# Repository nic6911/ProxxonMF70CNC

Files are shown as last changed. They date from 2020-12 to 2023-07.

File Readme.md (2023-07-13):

# Proxxon MF70 CNC
CNC conversion for the Proxxon MF70 based on 3D printed files.
Electronics embedded in Z-axis column !

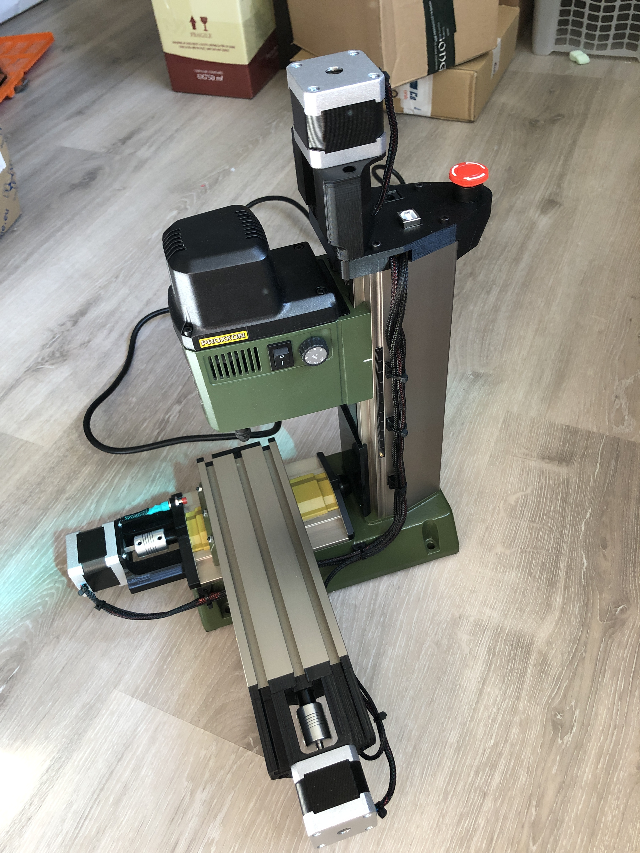
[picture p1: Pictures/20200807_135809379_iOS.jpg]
Machine


If you like then please

"Buy Me A Coffee" (https://bmc.link/nic6911w)

## BOM
Arduino UNO  
GRBL Shield w. 3 x drivers  
Braided cable sleeving  
Double adhesive tape for cable-tie mount  
3 x Alu flex coupler 5x5 mm shafts and outer measurements: 19x25mm  
E-stop button for 16mm panel cut-out. 23.5mm diameter button  
6 x F5-12M bearing  
3 x 7 mm push button switches for endstop SPST PBS-110  
12 x M3x6 for motor mount  
6 x M4x35 for mounting brackets  
6 x M4 SL nut  
3 x small screws for mounting Arduino  
3 x NEMA 17 stepper motors  
Wires and connectors as needed for switches and motors  

Printed parts:  
6 x cable_tie_mount  
3 x spacer_xyz  
1 of each of the remaining files  

## Software
GRBL and OpenBuilds Control software. My GRBL settings can be found in "grbl-settings-backup.txt"

## How To
Print the parts  
Measure up lengths of wires for motors and switches (make them somewhat longer than needed to be sure) and solder things up to get the extended cabling needed  
Disassemble the x, y and z-axis of the proxxon  
Remove the xyz handles from the lead screws  
F5-12M bearings goes in both ends on the x and y-axes and on the z-axis it there is one on both sides of the printed z-axis mount  
Only the original proxxon plastic part on the motor side is replaced on the x and y-axes  
A grooving in the 3D printed parts for the x and y-axes takes the metal plate from the original proxxon part  
Mount motors and end-switches on the x and y-axes motor mounts  
When a bearing has been placed in both ends of the x and y-axes the the motor mounts can be added to the x and y-axes (remember spacer and flex coupling)  
Make sure there is a little tension on the flex-coupler up against the spacer that pushes on the F5-12M bearing  
  
This work is licensed under a
[Creative Commons Attribution-ShareAlike 4.0 International License][cc-by-sa].

[][cc-by-sa]

[cc-by-sa]: http://creativecommons.org/licenses/by-sa/4.0/
[cc-by-sa-image]: https://licensebuttons.net/l/by-sa/4.0/88x31.png
[cc-by-sa-shield]: https://img.shields.io/badge/License-CC%20BY--SA%204.0-lightgrey.svg

Find more of my work here:  
https://youtube.com/user/wan46696  
https://www.instructables.com/member/nicengineering/

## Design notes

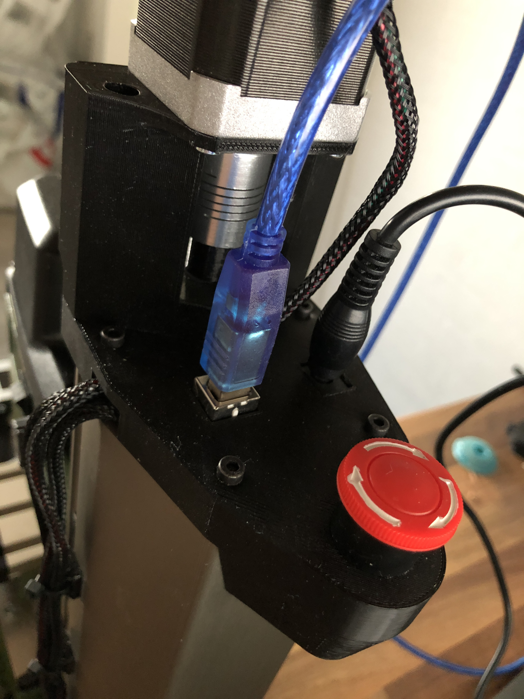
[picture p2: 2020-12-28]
Pictures/20200811_183554496_iOS.jpg

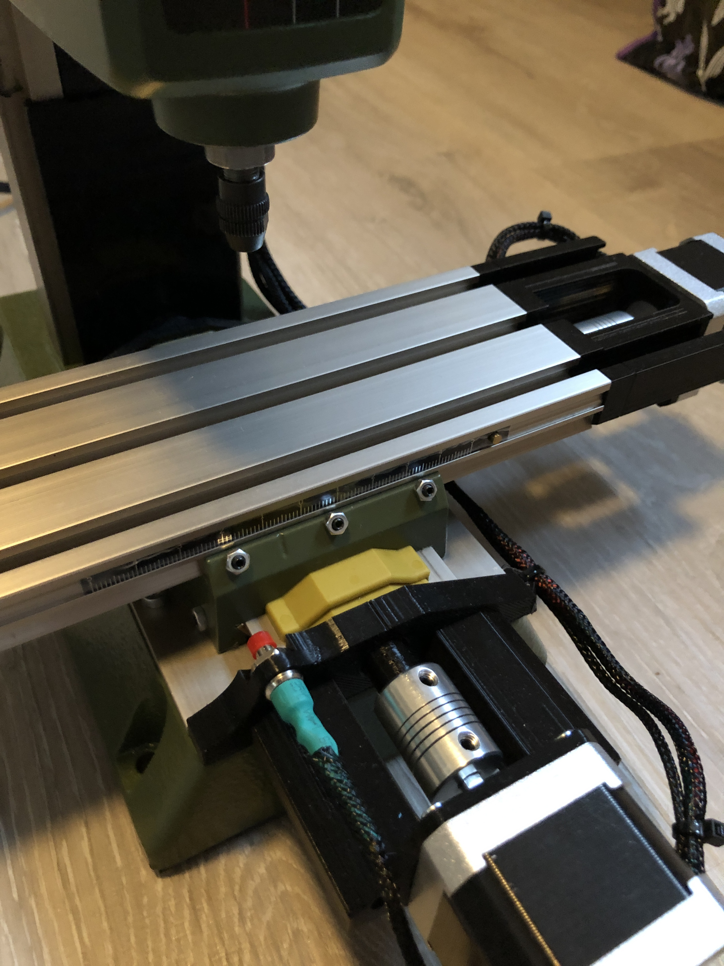
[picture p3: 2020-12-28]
Pictures/20200811_184021557_iOS.jpg

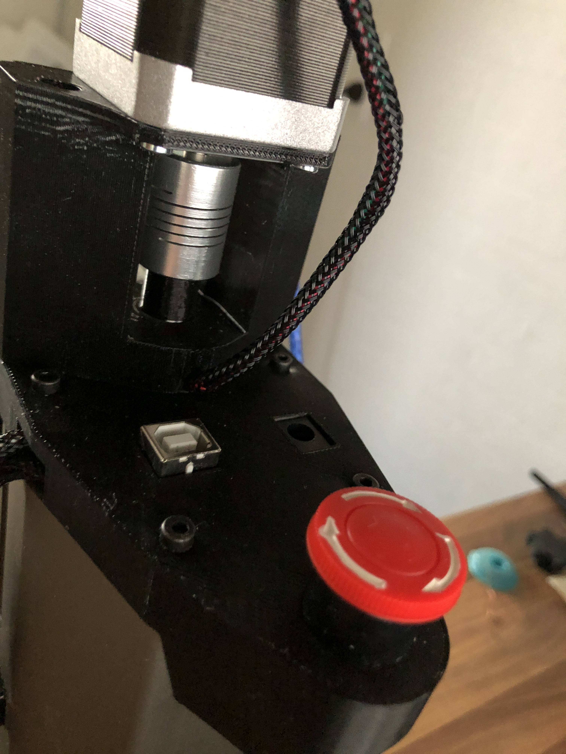
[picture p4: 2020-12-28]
Pictures/20200811_183607220_iOS.jpg

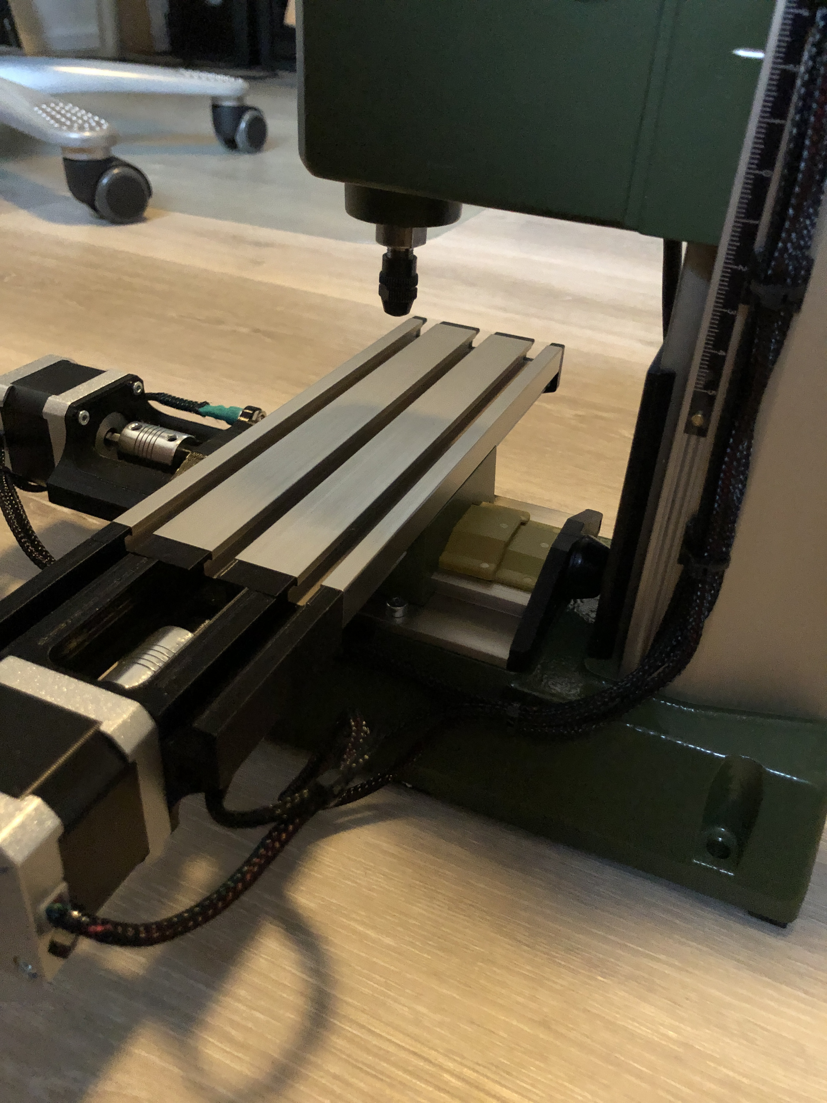
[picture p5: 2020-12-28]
Pictures/20200811_184040047_iOS.jpg

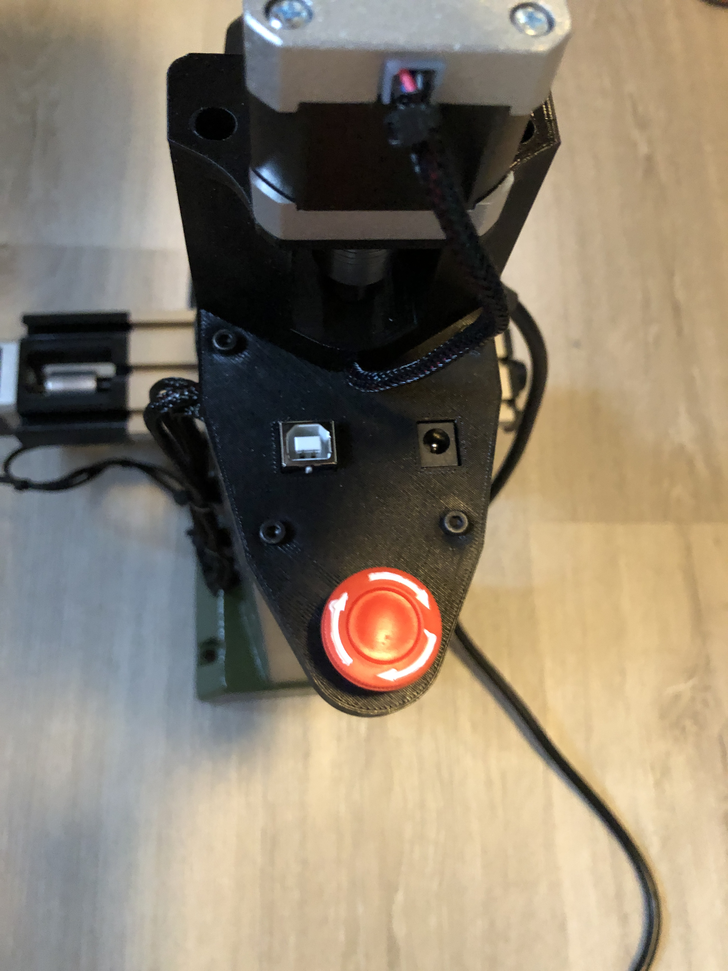
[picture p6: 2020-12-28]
Pictures/20200811_184008674_iOS.jpg

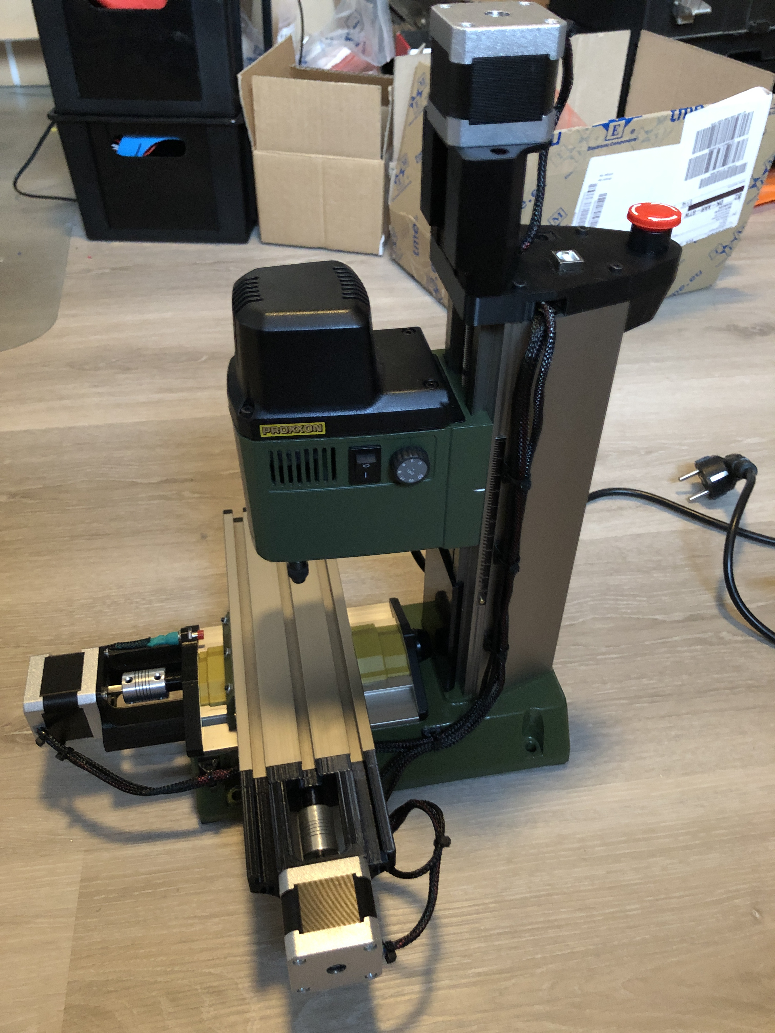
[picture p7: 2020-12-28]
Pictures/20200811_184046777_iOS.jpg

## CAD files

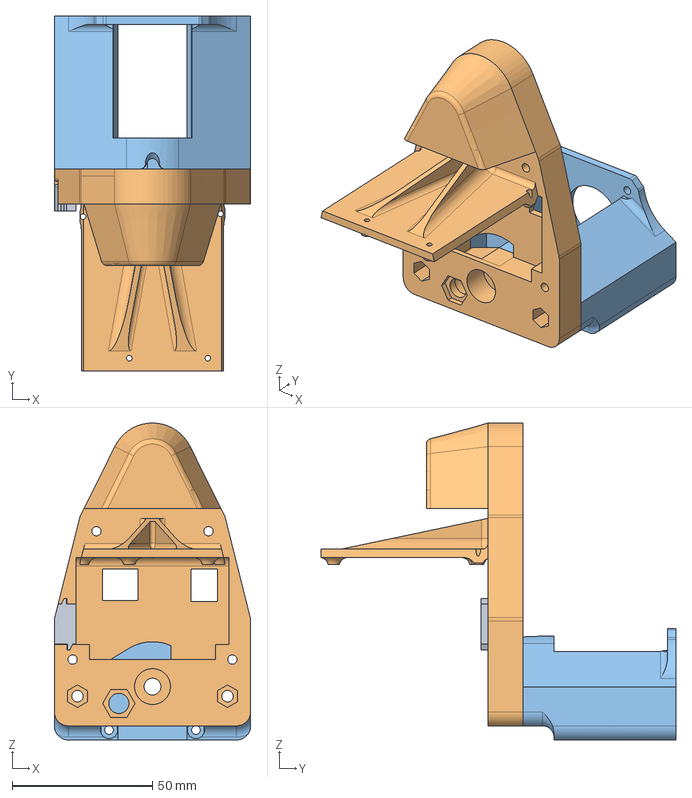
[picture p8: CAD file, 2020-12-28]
STEP/Z-axis_mount.step
70.0 x 126.5 x 113.0 mm

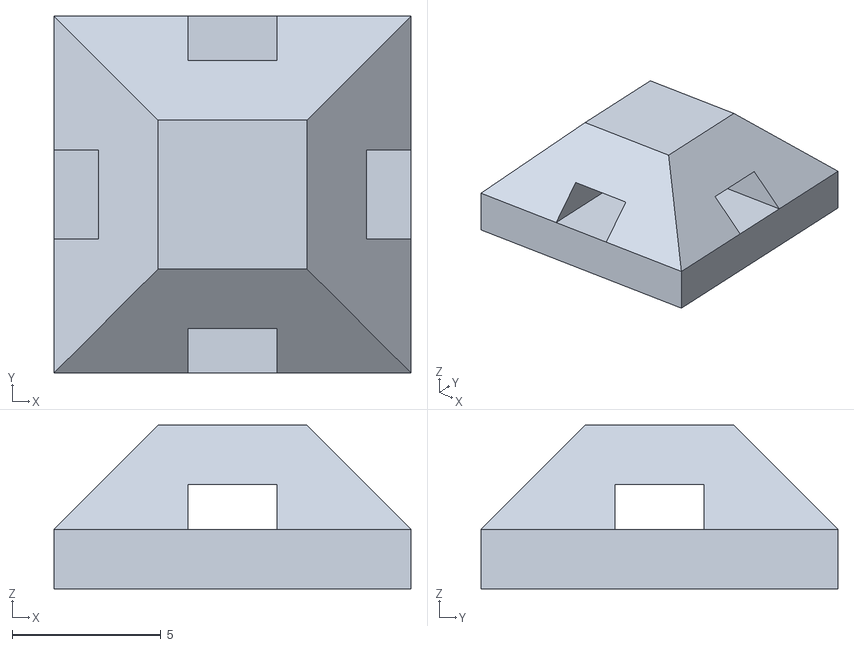
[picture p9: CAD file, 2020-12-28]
STL/cable_tie_mount.stl
12.0 x 12.0 x 5.50

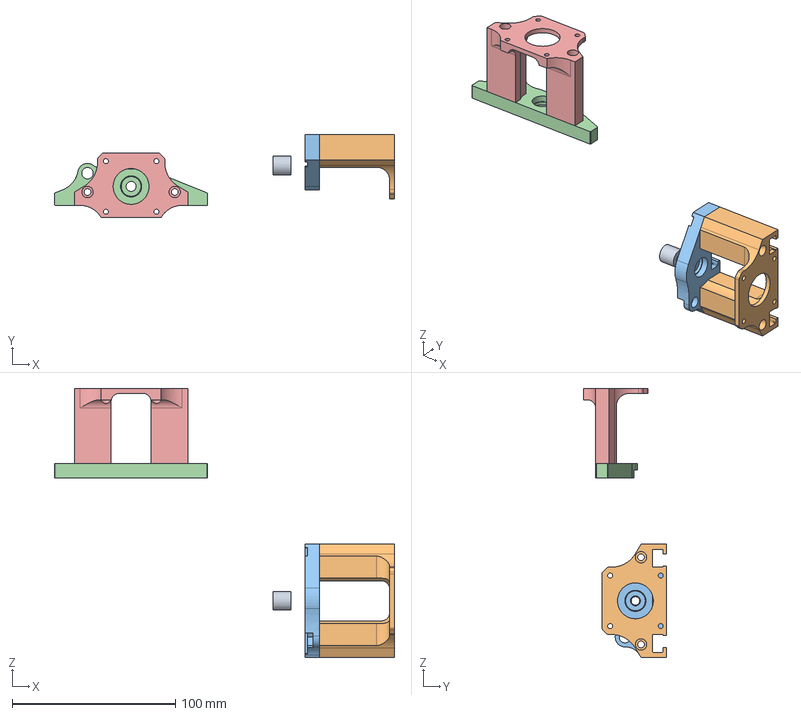
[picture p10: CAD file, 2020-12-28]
STEP/xy_mount.step
208.6 x 50.9 x 165.0 mm

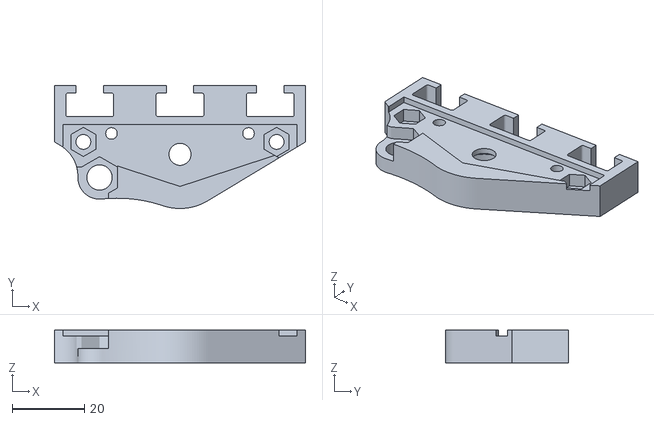
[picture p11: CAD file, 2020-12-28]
STL/x-axis_mount.stl
69.5 x 34.0 x 9.00

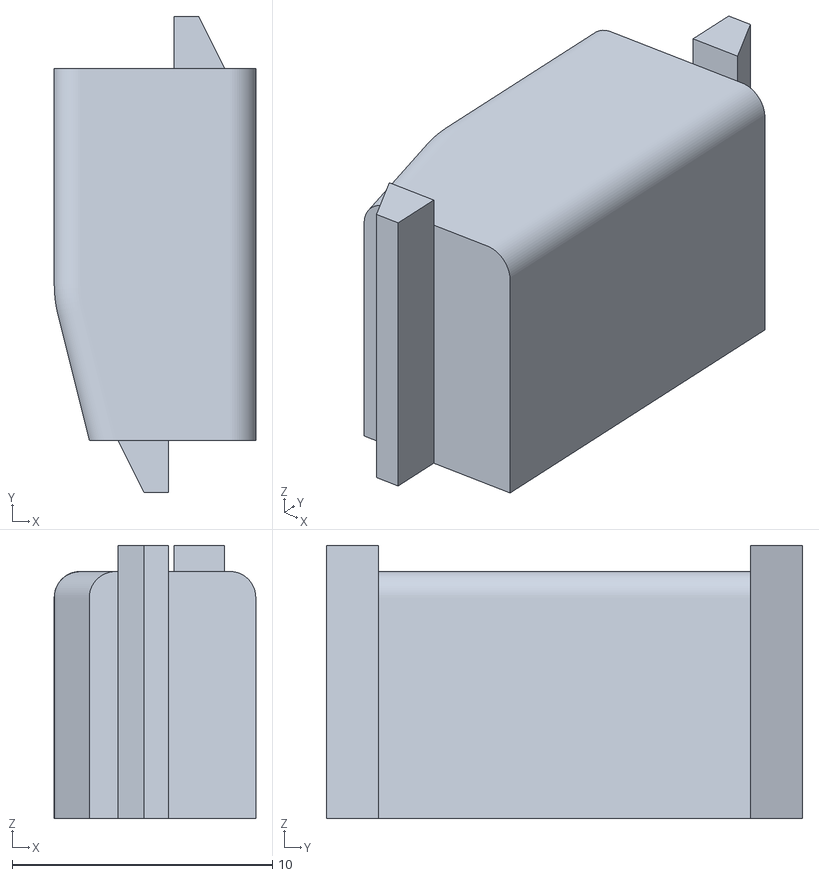
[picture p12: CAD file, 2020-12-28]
STL/z-axis_cablefix.stl
7.75 x 18.3 x 10.5

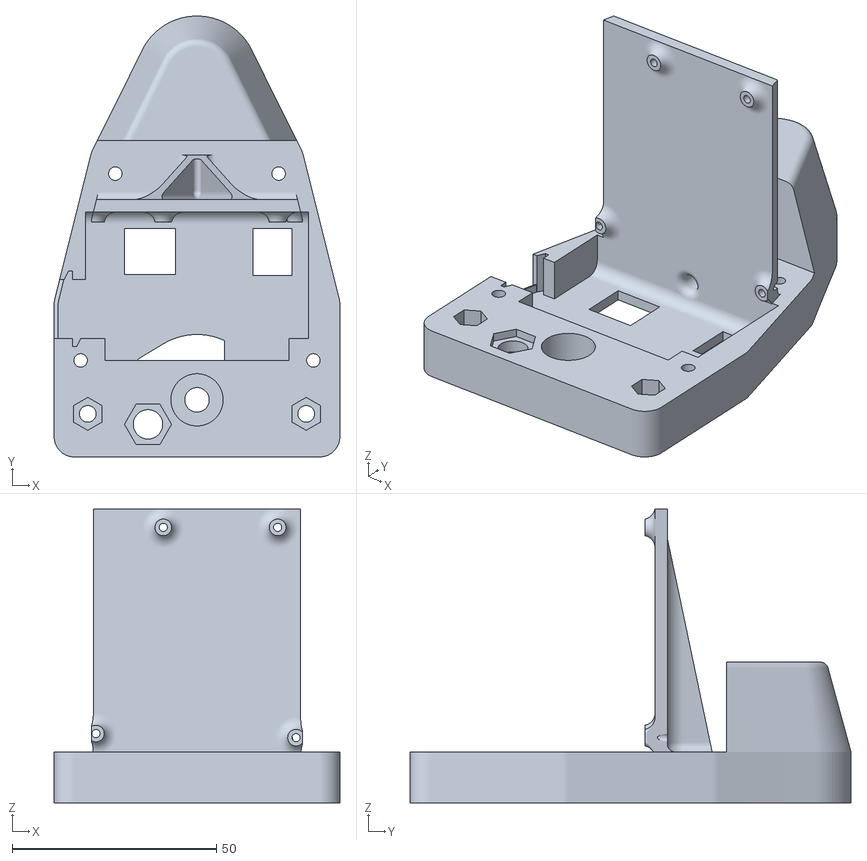
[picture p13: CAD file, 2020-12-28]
STL/z-axis_column.stl
70.0 x 108.0 x 72.0

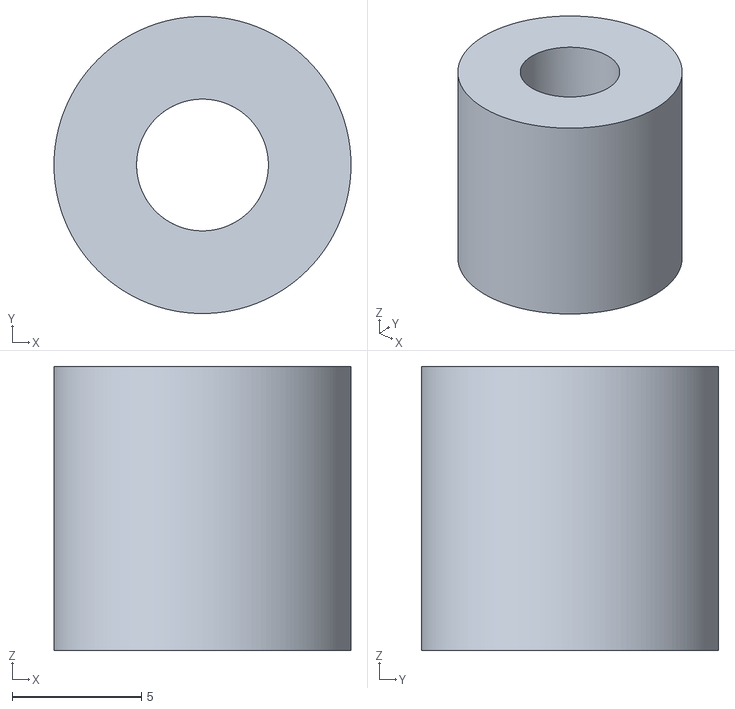
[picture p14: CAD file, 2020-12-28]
STL/spacer_xyz.stl
11.5 x 11.5 x 11.0

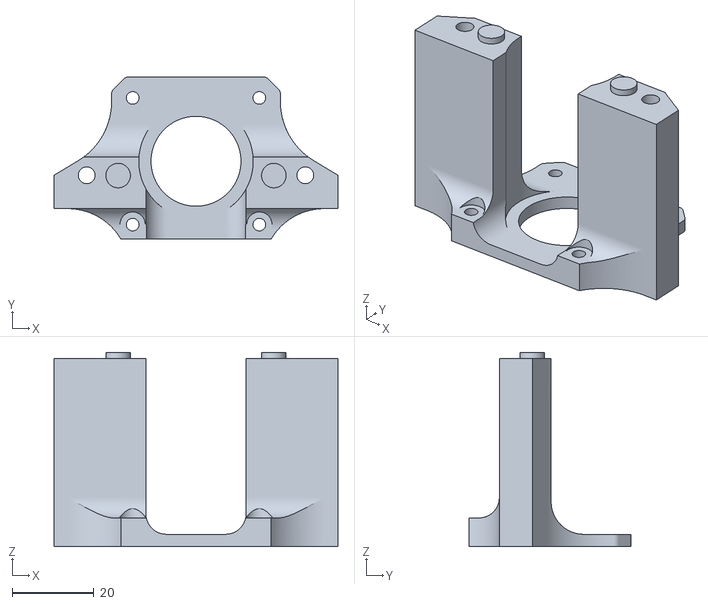
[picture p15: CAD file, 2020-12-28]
STL/y-axis_motor.stl
69.5 x 39.7 x 47.5

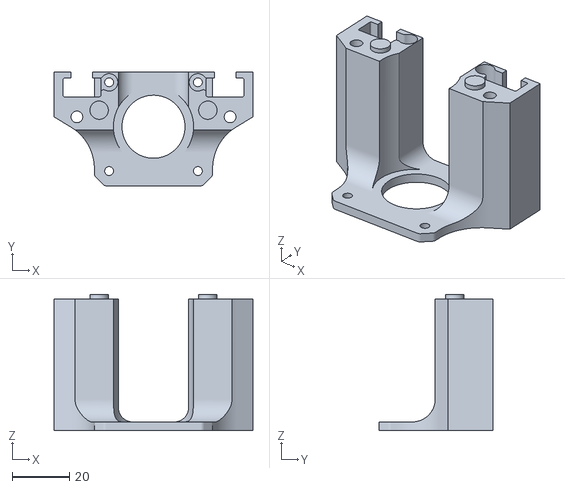
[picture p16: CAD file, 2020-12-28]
STL/x-axis_motor.stl
69.5 x 39.7 x 47.5

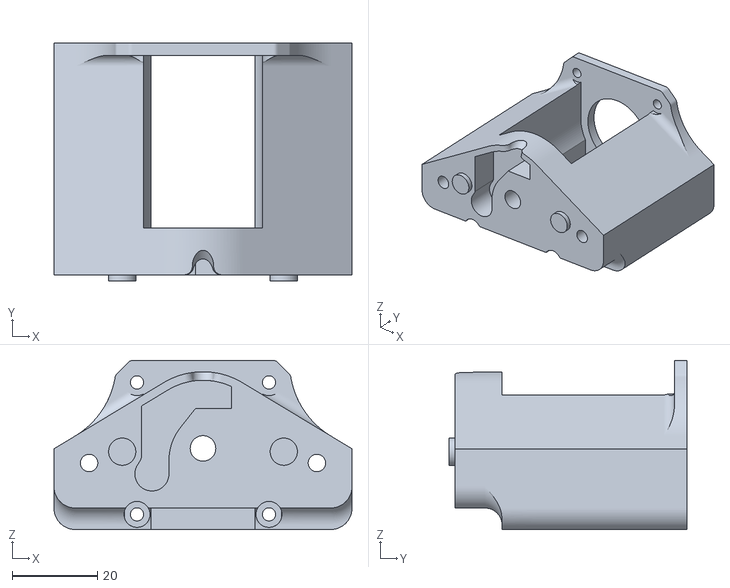
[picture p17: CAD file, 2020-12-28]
STL/z-axis_motor.stl
70.0 x 56.0 x 39.7

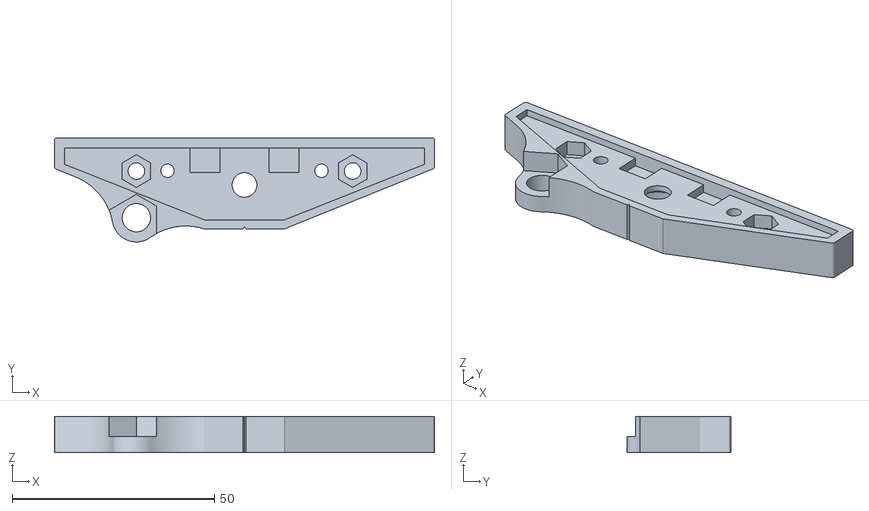
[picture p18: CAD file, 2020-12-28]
STL/y-axis_mount.stl
94.0 x 25.7 x 9.00

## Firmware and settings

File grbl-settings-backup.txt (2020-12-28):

$0=10  ;  Step pulse time, microseconds
$1=25  ;  Step idle delay, milliseconds
$2=0  ;  Step pulse invert, mask
$3=11  ;  Step direction invert, mask
$4=0  ;  Invert step enable pin, boolean
$5=1  ;  Invert limit pins, boolean
$6=0  ;  Invert probe pin, boolean
$10=1  ;  Status report options, mask
$11=0.010  ;  Junction deviation, millimeters
$12=0.002  ;  Arc tolerance, millimeters
$13=0  ;  Report in inches, boolean
$20=0  ;  Soft limits enable, boolean
$21=0  ;  Hard limits enable, boolean
$22=1  ;  Homing cycle enable, boolean
$23=3  ;  Homing direction invert, mask
$24=25.000  ;  Homing locate feed rate, mm/min
$25=200.000  ;  Homing search seek rate, mm/min
$26=250  ;  Homing switch debounce delay, milliseconds
$27=1.000  ;  Homing switch pull-off distance, millimeters
$30=1000  ;  Maximum spindle speed, RPM
$31=0  ;  Minimum spindle speed, RPM
$32=0  ;  Laser-mode enable, boolean
$100=6400.000  ;  X-axis steps per millimeter
$101=6400.000  ;  Y-axis steps per millimeter
$102=6400.000  ;  Z-axis steps per millimeter
$110=300.000  ;  X-axis maximum rate, mm/min
$111=300.000  ;  Y-axis maximum rate, mm/min
$112=300.000  ;  Z-axis maximum rate, mm/min
$120=10.000  ;  X-axis acceleration, mm/sec^2
$121=10.000  ;  Y-axis acceleration, mm/sec^2
$122=10.000  ;  Z-axis acceleration, mm/sec^2
$130=200.000  ;  X-axis maximum travel, millimeters
$131=200.000  ;  Y-axis maximum travel, millimeters
$132=200.000  ;  Z-axis maximum travel, millimeters

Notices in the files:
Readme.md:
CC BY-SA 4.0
